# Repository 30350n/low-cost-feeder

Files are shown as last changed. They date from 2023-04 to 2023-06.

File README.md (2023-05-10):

# Low Co$t Feeder

This is a cost optimized version of the original LumenPnP Feeders by
[Opulo](https://www.opulo.io/).

## Warning: This is still highly experimental, PCBs haven't been ordered/tested at all yet.

### Changes:

- **3.3V -> 5V mcu/logic supply**  
  The original RS485 transceiver costs 6-7€ in Qty 10, alternative parts that can be powered
  by 3.3V start at 3-4€. Similar 5V powered parts are already available for ~1€.
- **STM32F031 -> ATmega328PB**  
  The ATmega328P is just the first MCU I could think of that's 5V compatible and has just enough
  IO, is available in similar packages (TQFP and QFN), is similarly priced and should be able to
  run the photon firmware just fine. The ATmega328PB is not a drop in replacement, but has extra
  features (like UUID support) and is even cheaper.
- **470uF -> 100uF buck converter output capacitor**  
  There are very few 470uF 10V capable caps available in the specified package. The 470uF cap
  is also very overspecd, 100uF should be totally sufficient for the application. (The original
  value probably got copied straight from the datasheet example schematic.)
- **Countersinks -> [24882 solderable standoffs](https://www.digikey.com/en/products/detail/keystone-electronics/24882/9921841)**  
  Getting the countersinks done by the PCB manufacturer is probably way to expensive,
  especially for low qty orders. The standoffs would add a cost of ~2.5€ per board.
  Alternatively it might be possible to use a 3D print with standard M3 nuts/heat set inserts,
  glued to the PCB in their place.  
  Adding the countersinks to the holes yourself is still possible too.
- **Option to bypass the onboard SMPS** (thanks @FL140 for the idea!)  
  Added a 0R resistor to bypass the onboard SMPS for **users of +12V machines**. This should
  save 1-2€ in components and might also have some other benefits, like better EMC.  
  **If this option is being used, the DRV8837 motor drivers should be replaced with +12V
  tolerant ones, for example DRV8220.**

## LumenPnP Feeders
The LumenPnP Feeders are open source pick and place feeders to aid in [Mid-Scale Manufacturing](https://stephenhawes.com/level-2-manufacturing/).

LumenPnP Feeders

LumenPnP Feeders are available for sale on the [Opulo Website](https://www.opulo.io/). If you build or buy one, please help the project by documenting bugs with a GitHub issue.

The LumenPnP Feeders run [Photon](https://github.com/photonfirmware/photon), an open source firmware project for pick and place feeders. The popular pick and place control software [OpenPnP](https://openpnp.org/) has Photon support built in, so it's easy to get going with the LumenPnP feeders using your existing OpenPnP setup. These feeders are designed to work with the [LumenPnP](https://opulo.io/products/lumenpnp).

The development process is being cataloged in a series of videos. A playlist of these can be found [here](https://www.youtube.com/playlist?list=PLIeJXmcg1baLBz3x0nCDqkYpKs2IWGHk4).

### Documentation
Feeder user documentation can be found on the [Opulo Docs Page](https://docs.opulo.io/). Open Hardware Assembly instructions can be found at [ohai.opulo.io](https://ohai.opulo.io/).

### Community
Discussion about the project happens on the [STR Discord server](https://discordapp.com/invite/TCwy6De)!

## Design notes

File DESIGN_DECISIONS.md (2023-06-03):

# LumenPnP Feeder Design Decisions

This page aims to illustrate the design decisions behind the LumenPnP Feeders. The design process started in early 2020, and has seen hundreds of iterations and approaches. This page gives background about why things are done the way they are, to help communicate to folks new to the project what has been tried, and why it was not chosen.

## Overview

The LumenPnP feeders are a mostly 3D printed tape feeder capable of reliably feeding 0402 components. They are designed to easily mount to a 20mm x 20mm v-slot aluminum extrusion. There are two motors in the system: a drive motor and a peel motor. The drive motor is a right-angle N20 motor with an encoder, giving us incredibly high resolution control of the motor's position. The peel motor is a standard N20 motor that peels film using a few 3D printed gears. The feeder has two buttons for tape loading and manual control. A third button puts the feeder into bootloader mode, allowing anyone to flash new firmware using a common FTDI USB to UART converter.

Feeders connect to power and communication when mounted to a rail through a "slot." Slots all connect back to a LumenPnP motherboard using an IDC cable. Each slot has a 1-Wire EEPROM onboard which holds the slot's address. This address is used to tell OpenPnP where a certain feeder has been mounted. All communication back to the motherboard happens over RS-485 using the Photon Protocol.

## Drive Subsystem

The Drive Subsystem is in charge of moving the tape forward at very precise increments. A right-angle N20 motor with a 1:1030 ratio gearbox was chosen for this task. This gear ratio provide a tremendous amount of torque for the size of the motor. An encoder on the back shaft of the motor has 14 ticks per revolution, which results in a theoretical 8.8 micron tape movement resolution. Of course, there are many other factors at play that reduce how precise the feeder is actually able to position tape, but the encoder is plenty precise enough for our application.

### Why not stepper motors?

While stepper motors are great for high-precision movement in systems like a 3D printer, they're less optimal for a small device like a feeder.

One of the main considerations with a feeder design is its width. The thinner a feeder is, the more of them you can fit on a given machine, and the more useful they become. Steppers thin enough to fit within a reasonably sized feeder suffer from a lack of torque, and would likely skip steps trying to advance tape. This is especially true when using microstepping, which would likely be necessary for the small movements required in a feeder.

Steppers also lack absolute positioning. All of their movements are relative, and without an encoder or a driver that supports skipped-step detection, we wouldn't know if the stepper has skipped steps.

It's possible to use a pancake stepper motor with a high-torque gearbox and a driver like the TMC2209 for skipped step detection, but a small DC motor with an encoder used fewer parts and had fewer points of failure.

### Why not an external gearbox/gear system?

Many feeder designs utilize a custom gear system that is mounted within the feeder itself. This can provide incredibly high torque if the gearing ratio is high enough.

We chose to avoid this for two main reasons. The first is that we trust the metal gearbox in a right-angle N20 motor much more than a (likely plastic) gear system that we designed. The N20 "standard" is ubiquitous and thoroughly tested. If we can keep our entire gearing system in metal gears, and in an easily sourced, highly tested part, it's a huge win for accessibility and reliability.

The second reason is ease of sourcing/building. If we used "off the shelf" nylon gears, not only would using a pre-existing gear be a huge design limitation, but also they might be difficult to source for the hobbyist or builder. If we went with totally custom gears, this makes the sourcing issue even worse. And even if folks could print them at home, the resolution required for the precise tape movement would be so high that the print would likely have to be SLA.

### Why not an encoder on the drive wheel itself?

In early versions of the feeder, we used a reflective sensor to watch for voids in the drive wheel. Putting our closed-loop feedback system on the last step of the drivetrain is great in theory. Monitoring as close to the actual metric you're controlling will provide a tighter coupling between your independent and dependent variables. There are three reasons we ended up switching to a magnetic encoder on the motor's back shaft.

The first is the low precision of the reflective sensor. The low/high and high/low threshold transition point of the reflective sensor was entirely dependent on how precise the cutout of the drive wheel was. Given that the wheels are made from PCBs which do not have a high tolerance with edge cuts, precision was very low. The sensor itself was also very noisy, requiring lots of signal processing to provide a useful signal. Early tests showed that *each feeder* would need its own custom calibration, which would be a tremendous effort, and discourage hacking.

On the other hand, a magnetic encoder provides 14 ticks per revolution of the motor. Because we are gearing down the motor with such a high ratio, we get an astronomically high precision of our gearbox output.

`14 ticks / 1 motor revolution * 1030 motor revolution / 1 gearbox revolution = 14420 ticks / 1 gearbox revolution`

This means that with a 128mm wheel circumference (32 teeth with 4mm spacing), we have a theoretical 8.877 micron tape positioning resolution. In practice, small tolerance stackups in the gearbox and drive wheel geometry mean we aren't this precise with actual tape position, but it's much better than the 200-500 or so micron resolution we saw with the reflective sensor.

The second reason is that any backlash error in the N20 gearbox can be accounted for by only positioning **from one side**. Backlash is only evident when there exists a reversal of the axis direction. If we only ever approach our position from one direction, backlash does not play into the tape positioning. Even when feeding backwards, we simply overshoot the final position, then approach again from the same direction.

The third reason is that with an encoder, we can move arbitrary distances. With a reflective sensor/slotted drive wheel, our resolution is limited to how far apart we've spaced the slots. With an encoder, we can command the feeder to move effectively any distance (provided it's a multiple of 8.877 microns!). This means feeding 1mm increments is fundamentally the same as feeding 4mm increments.

However, this all assumes that the encoder on the output wheel is comprised of a slotted PCB with a reflective sensor. Very thin encoder wheels and sensors exist, and might be a reasonable option for feeder tape positioning. We decided against this approach due to the lower resolution, cost, and likely need for customization that would make homebrew builds more difficult. They're also susceptible to errors due to light bleed.

### Why glue the shaft collar to the Drive Wheel?

Ideally, affixing the shaft collar to the Drive Wheel uses mechanical coupling, as glue can be finicky. We tried a screw-affixed design, but in order to have the screws fit without hitting the motor the PCB needed to be countersunk. That countersink added a bump to the opposite side of the board. When the shaft collar was mounted to it, we saw a very high sinusoidal variation in the tape position throughout the rotation of the wheel because the collar and wheel weren't coplanar anymore. Glue ended up being the most consistent approach in terms of tape positional accuracy.

We used to have a  D-shaft cutout in the center of the wheel, we found that it was over-constraining the glueing process so we removed it. If we're going to glue, we should reference it to the outer profile of the teeth as much as possible, which is really what matters in this application.

## Peel Subsystem

The Peel Subsystem is comprised of a standard N20 motor with a 1:210 gear ratio, with a printed worm gear attached to the output shaft. This worm gear interfaces with a gearbox used for peeling the film. The two straight gears that perform the peeling are mounted with a positive interface, ensuring the frame holding them in place is constantly applying pressure between them. This interface is what grips the film and pulls it away from the tape.

### Why not passive peeling?

Passive peeling mechanisms have been shown to work in many instances. Allowing the force of the drive motor to remove and/or guide the film away from the tape is a great way to reduce the part count. We ultimately decided to use a dedicated peel motor instead of a passive approach for a number of reasons.

First, in our tests we found that passive film peeling methods were only reliable with highly-tuned 3D printer settings to make a working geometry. Not only do we want the design to be possible to be built at home, but it also needs to be straightforward to build in a scaled-up manufacturing setting. Scrapping a high volume of prints because of not hitting a very tight dimensional tolerance would be a frustrating and expensive experience for builders and Opulo alike.

Second, we found that passive film peeling worked better with certain types of tape, and worse with others. In situations where the film is lightly attached to the tape, depending on the method of passive film removal, *both* sides of the film could come unstuck from the tape, jamming the feeder. In the situation where the adhesion was high between the film and tape, the drive motor had to work much, much harder to both drive the tape and remove the film.

Our approach not only ensures there's plenty of force present pulling the film from the tape, but it also accommodates any type of tape as defined by the EIA-418 standard. Even if the film is strongly adhered to the tape, or stretches easily and requires more peeling, the flexture holding the peel gears together allows film to slide between the gears when overdriven.

### Aren't you worried about wear/creep with plastic gears and tensioning?

At first, we were. But the benefits of being printable are high, allowing the design to be more accessible. We ran lifetime tests with the peel mechanism and had very good results.

We tested the peel gear box to a quarter million feed cycles, resulting in a kilometer of tape fed, and saw no failure of the gearbox's ability to peel film. There is slight initial wear of the gears that is present within the first 10k cycles, but after this the system hits steady-state.

Even then, we ensured that this part is easily replaceable if need be. It's easily printable at home, and can be replaced in less than a minute with only two screws.

### Why no tension sensor?

We found that it wasn't necessary. Many feeder designs use a switch to detect when the film has reached a sufficient tension, but with our flextured peel gear box, we can simply overdrive the peel mechanism and the film will slip through the gears once it's been peeled fully and can't move any more.

## Voltage Rails

The feeders are powered by 24 volts on the slot. They step this down to 10 volts using a buck converter, then down to 3.3 volts using an LDO.

### Why 24 Volts Bus Voltage?

24 volts was chosen for the bus voltage for a few reasons. First, it's already on the motherboard given that it's the voltage of the power supply for the machine. Second, a higher voltage allows us to send more power over thinner wire. We wanted to use IDC connectors on the slot harness due to the form factor of the slot, and need for many connectors on a single cable. Using 24 volts lets us send more power for a given current limit of the cable.

Next comes the 10 volt buck converter. The N20 motors accept up to 12 volts, but the DRV8837 H-Bridge motor driver chips only accept up to 11 volts. This chip was chosen as the motor driver due to its cost and availability. Other chips with a higher acceptable voltage of course exist, but are much more expensive or can be hard to source. We also looked for 24 volts motors, but the N20 standard does not seem to accept a voltage higher than 12 volts.

Lastly is the 3.3 volt LDO. This is used for the microcontroller, encoder, switches, LEDs, etc.

## Slot Addressing

Each feeder is loaded into a slot, which is a small 3D print and PCB with a 1-Wire EEPROM. When the feeder is loaded, it reads the slot address from the EEPROM. This is what the host uses to address the feeder in most instances.

### Why is this even necessary?

This system isn't strictly necessary for feeders to operate. But it does allow the host to be much more intelligent about how it handles feeders.

If we neglected to have a slot address, then we'd be operating purely on the feeder's UUID. Assuming we've solved the problem of feeder discovery once inserted, the host would have no idea *where* the feeder is after it's mounted. This means that the user needs to manually jog the head to the feeder every time it's inserted in order to set pick position.

If we neglected to have a feeder UUID and only knew what location a feeder was mounted into, we wouldn't be able to keep track of what part the feeder has; we'd just know where it is.

By having both a feeder UUID, and an address for each location, we can dynamically find where a feeder has been inserted and know what part is at that location.

### Why not use voltage dividers?

Voltage dividers are a very inexpensive method of setting a specific value for a microcontroller. The EEPROM might seem like overkill to hold a single address. We chose to avoid voltage dividers for a couple reasons.

Firstly, the likelihood of error was very high. If we want to support up to 255 devices on the bus, we'd need that many addresses, and that many discrete voltages from the divider. With a 3.3 volt starting voltage, that means we have 12.9 millivolts per address. The precision of the resistors used would have to be incredibly high to support this resolution, and we'd be assuming no voltage loss in the spring-pin interface.

Voltage dividers also require that the feeder has an ADC as opposed to just a GPIO pin used for 1-Wire communication.

### Why not use an I2C/SPI EEPROM?

Provided that we were able to find a spring pin connector with two more wires, we absolutely could have! The benefit of 1-Wire is that it only requires one pin for both communication *and* power. I2C devices would require three dedicated pins: SDA, SCL, and VCC. The spring pin interface we chose that allows the entire feeder geometry to work only comes with up to 5 pins. With four already used for RS-485 and power, the one left is allocated to the EEPROM.

## Host Communication

At the top of the communication stack is the host. The host is what decides which feeder needs to feed, and when. OpenPnP acts as the host in this scenario. OpenPnP sends M485 commands to Marlin, and gets data from feeders back as a result. A custom OpenPnP feeder type `PhotonFeeder` supports common Photon commands such as feed, self-identify, initialize, or check for feed status.

Next comes Marlin. Marlin is the firmware on the LumenPnP and relays commands to feeders along an RS-485 bus that connects to every slot. It sends data using the Photon Protocol. A new M command for Marlin's gcode interface, M485, allows a host to send data down the RS-485 bus using Photon, and thereby communicating with feeders.

### Why RS-485?

RS-485 is an electrical standard that is widely used, particularly in industrial environments. Being a differential signal, electromagnetic interference that affects both data lines does not affect the signal integrity.

### Why not CAN?

CAN would have also been a great option for feeder communication. The decision to stick with a custom protocol over RS-485 ended up coming down to the large size of a CAN frame. The arbitration system is a bit overkill for a system with only two types of devices. Bit stuffing, plus a long CRC and end of frame section make the frame lengthy, keeping the bus noisier than necessary. CAN would have worked just fine, we just preferred to spin our own protocol that was exactly what we needed.

### Why not MODBUS?

MODBUS is a great, royalty-free protocol, and does fulfill many project requirements. There are two main reasons we decided to implement our own protocol.

The first is that MODBUS only supports the host initiating a message. We wanted to allow the possibility that feeders themselves can initiate communication back to the host, instead of only ever waiting to be queried.

The second reason is that we are not only working with a device ID, we are working with its slot address, which acts as its location on the machine. Although we could store address data in the feeder and query it with MODBUS, we couldn't scan every possible feeder ID easily. With Photon, we simply ping each of the 50 possible addresses and see which IDs come back. MODBUS is designed for systems where the ID of each device on the bus is known, and likely immutable. Feeders are easily swapped, and need to be easily recognized once inserted. This flexibility is what Photon provides.

## Microcontroller

An STM32F031C6T6 was chosen for the feeder's microcontroller. There were a few requirements of the chip in order to hit the project goals:

* Available and generally low cost (two variables that are a moving target in our modern semiconductor market)
* At least 1 UART for RS-485
* Sufficient GPIO for buttons, LED, encoder, etc.
* Internal UUID for identification by the host

As a bonus, the chip's sibling, the STM32F031K6U6, has the same die as the C6T6 but with a smaller package. This means that by using the smaller chip's GPIO count as a constraint, we have a binary-compatible drop in replacement part to help alleviate availability issues.

Although a separate EEPROM chip or a software-defined UUID could solve the same problem as having a factory-burned UUID, having it in the chip prevents UUID erasure upon reprogramming, and fewer parts in the BOM.

## ID Fiducial Board

There's a small board on the nose of the feeder with three fiducials on it. The center one is for identifying location, and the other, smaller fiducials on either side identify what type of feeder it is.

**This is not currently used. This board was shipped with all feeder hardware to support potential future features.**

### Can it be used for setting pick position?

It could be used for *generalized* pick position. In general, there's too much variability in the precise placement of the PCB in the print from human error and print defects. If OpenPnP can scan for the fiducial and then apply a general offset to find the broad pick position, computer vision can find the precise pick position, provided it's paper tape. Plastic tape would likely need the precise pick position set manually.

### Can it be used for identifying feeder width?

Absolutely! The distance the two smaller fiducials are away from the larger centered one encodes what feeder type, or width, it is. Ideally the firmware image is the same across feeder widths, and it can't hurt to have the fiducial encode that information. OpenPnP doesn't actually care that much what width a feeder is if the fiducial <-> pick position offset is set correctly.

### Can it be used for setting slot location?

It can, but it might not be useful in most circumstances. In a world where slots are always mounted in the same location, OpenPnP could always know where the slot locations are on a LumenPnP. However, if builders have a different slot setup, or folks trying to squeeze out every last mm of feeder space are adjusting their slot locations to accommodate wider feeders, it could be useful. OpenPnP could use vision across a given Y position and in conjunction with the slot addresses of the feeders it found over RS485, automatically set slot positions.

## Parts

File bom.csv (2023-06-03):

Part Name | Image | Quantity | Part Type | Source 1 | Source 2 | Optional | Note
frame |  | 1 | FDM | Download all 3D printed parts at the link at the top of the page.
drive-motor-bracket |  | 1 | FDM | Download all 3D printed parts at the link at the top of the page.
drive-motor-cover |  | 1 | FDM | Download all 3D printed parts at the link at the top of the page.
peel-gear-frame |  | 1 | FDM | Download all 3D printed parts at the link at the top of the page.
peel-gear |  | 2 | FDM | Download all 3D printed parts at the link at the top of the page.
peel-worm-gear |  | 1 | FDM | Download all 3D printed parts at the link at the top of the page.
release-lever |  | 1 | FDM | Download all 3D printed parts at the link at the top of the page.
spool-holder |  | 1 | FDM | Download all 3D printed parts at the link at the top of the page.
thimble |  | 1 | FDM | Download all 3D printed parts at the link at the top of the page.
slot-bracket |  | 1 | FDM | Download all 3D printed parts at the link at the top of the page.
PLA-filament | https://90a1c75758623581b3f8-5c119c3de181c9857fcb2784776b17ef.ssl.cf2.rackcdn.com/611532_989269_03_front_zoom.jpg | 1.2 | FIL | https://www.microcenter.com/product/611532/inland-175mm-black-pla-3d-printer-filament-1kg-spool-(22-lbs) |  |  | Units in kg. Print both nozzle-rack and 2x z-gantry in a black color. Print top-light-mount and bottom-light-mount in a white color.
M3-hex-nut | https://www.mcmaster.com/mvD/Contents/gfx/ImageCache/905/90592A085p1-b01-digitall@4x_636713274654410000.png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 | 11 | FST | https://www.mcmaster.com/90592A085/ |  |  | ISO4032
M5-t-slot-nut | https://www.mcmaster.com/mvD/Contents/gfx/ImageCache/946/94645a102-@1x_637691238154449529.png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 | 1 | FST | https://www.mcmaster.com/94645A102/
M3x12mm-flat-head | https://www.mcmaster.com/mvD/Contents/gfx/ImageCache/920/92095A181p1-b01-digitall@2x_636621119072096469.png | 2 | FST | https://www.mcmaster.com/92095A181/
M3x14mm-flat-head | https://www.mcmaster.com/mvD/Contents/gfx/ImageCache/920/92095A168p1-b01-digitall@2x_636621121852034289.png | 2 | FST | https://www.mcmaster.com/92095A168/
M3x15mm-flat-head | https://www.mcmaster.com/mvC/Contents/gfx/ImageCache/912/91292a115-@4x_637619456157301135.png | 10 | FST | https://www.mcmaster.com/91292A115
M5x10mm-socket-head | https://www.mcmaster.com/mvD/Contents/gfx/ImageCache/901/90128a234-@4x_637648793587366175.png | 1 | FST | https://www.mcmaster.com/90128A234/ |  |  | ISO4762
M3x8mm-self-tapping-flat-head | https://www.mcmaster.com/mvD/Contents/gfx/ImageCache/958/95893a189_5471d27b-8a4e-4cd5-bc6c-43c4b611d281@2x_637901339772075158.png | 1 | FST | https://www.mcmaster.com/95893A189/
mobo |  | 1 | PCA |  |  |  | Click link above to download source. 1.6mm PCB, 2 layer, Black Soldermask, White Silkscreen, ENIG
slot |  | 1 | PCA |  |  |  | Click link above to download source. 1.6mm PCB, 2, layer, Black Soldermask, White Silkscreen, ENIG
drive-wheel |  | 1 | PCB |  |  |  | Click link above to download source. 1mm PCB, 2 layer, Any Color Soldermask, White Silkscreen, ENIG
light-diffusion |  | 1 | PCB |  |  |  | Click link above to download source. 0.6mm PCB, 2 layer, Matte Black Soldermask. Board has no silkscreen or copper. Only soldermask on the front and back.
photon-8mm-fid |  | 1 | PCB |  |  |  | Click link above to download source. 1mm PCB, 2 layer, Matte Black Soldermask, White Silkscreen, ENIG
slot-harness |  | 1 | CHA |  |  |  | Click link above to download source
spring | https://www.leespring.com/sites/default/files/inline-images/226%C3%97113_Compression_HomePage_2.jpg | 1 | MISC | https://www.leespring.com/compression-springs?search=LC026C06M
n20-motor | https://www.makerfabs.com/image/cache/makerfabs/N20%20DC%20Gear%20Motor/N20%20DC%20Gear%20Motor_3-1000x750.jpg | 4 | MISC | https://www.servocity.com/110-rpm-micro-gear-motor/ |  |  | 1:210 gear ratio.
right-angle-n20 | https://sharvielectronics.com/wp-content/uploads/2022/06/N20-3V-50-RPM-Micro-Metal-Gear-Motor-With-Encoder_-Sharvielectronics.jpg | 2 | MISC | https://www.aliexpress.com/w/wholesale-worm-n20-encoder.html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 |  |  | 14-tick per revolution encoder. 1:1030 gear ratio gearbox.
shaft-collar | https://m.media-amazon.com/images/I/51dc5w8vG5L._AC_.jpg | 2 | MISC | https://www.amazon.com/gp/product/B01EA912P8/ref=ppx_yo_dt_b_asin_title_o09_s00?ie=UTF8

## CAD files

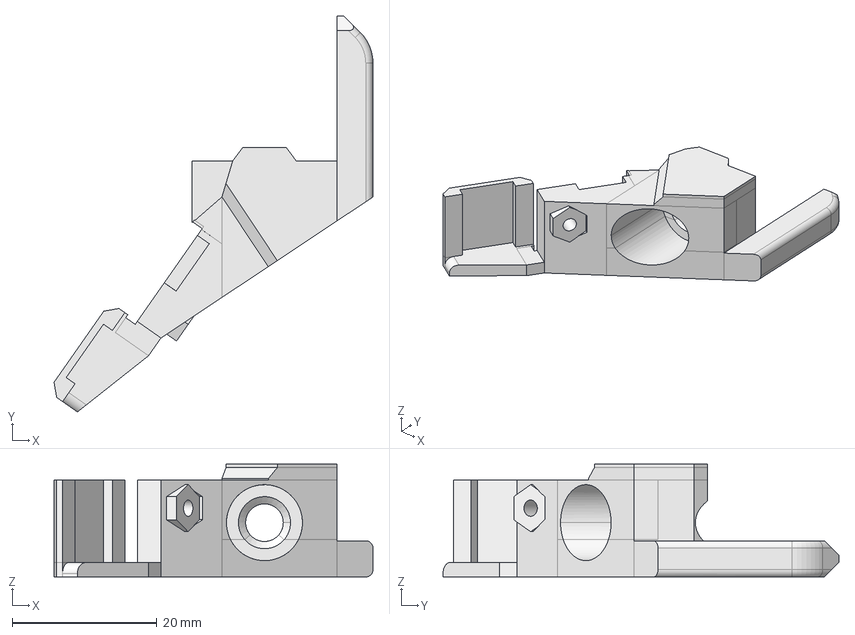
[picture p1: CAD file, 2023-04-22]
cad/FDM/slot-bracket.FCStd
44.1 x 54.7 x 15.6 mm

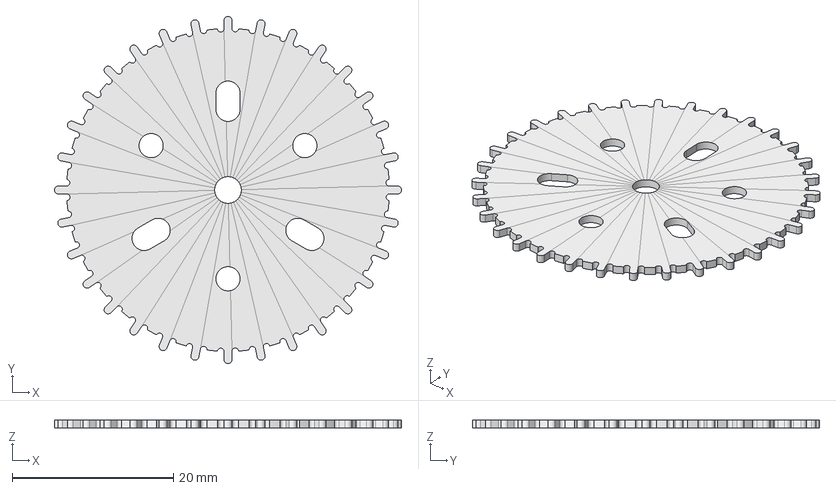
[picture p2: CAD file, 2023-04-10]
cad/indexing-wheel.FCStd
43.0 x 43.0 x 1.00 mm

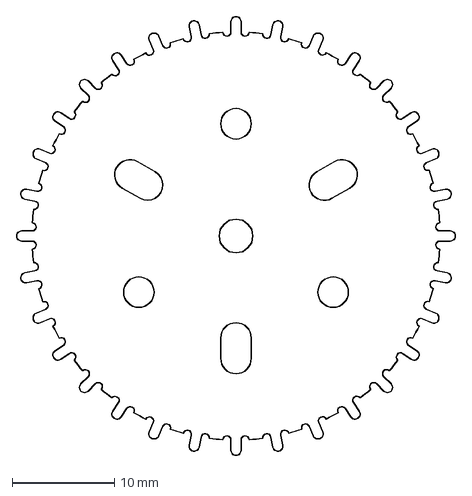
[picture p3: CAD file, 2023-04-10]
pcb/indexingWheel/indexingWheel-outline-rev06.dxf
43.0 x 43.0 mm

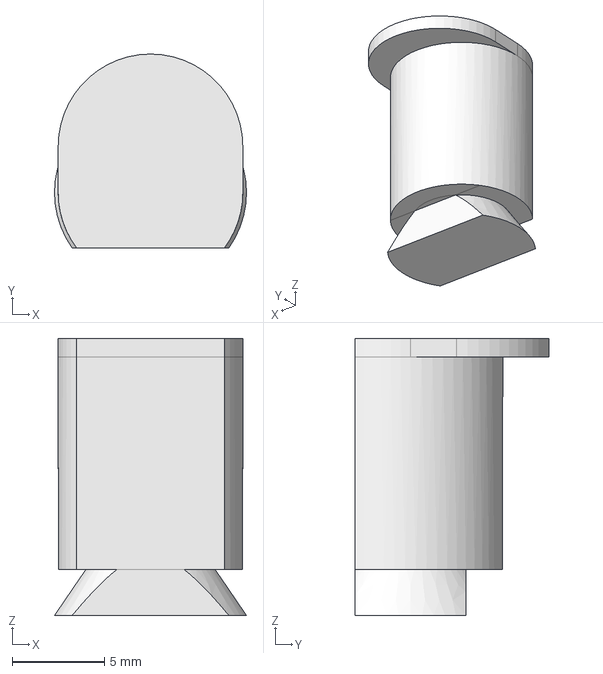
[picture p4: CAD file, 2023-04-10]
cad/FDM/thimble.FCStd
10.4 x 10.5 x 15.0 mm

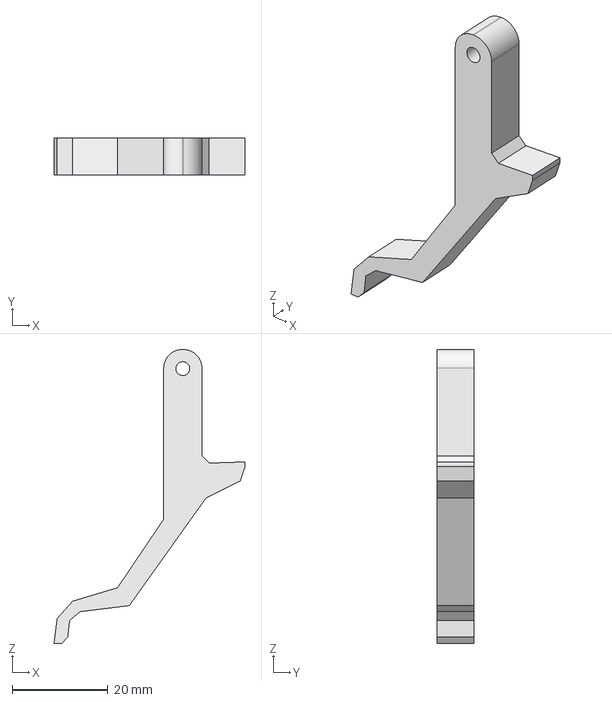
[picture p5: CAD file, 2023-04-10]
cad/FDM/release-lever.FCStd
39.9 x 7.75 x 61.5 mm

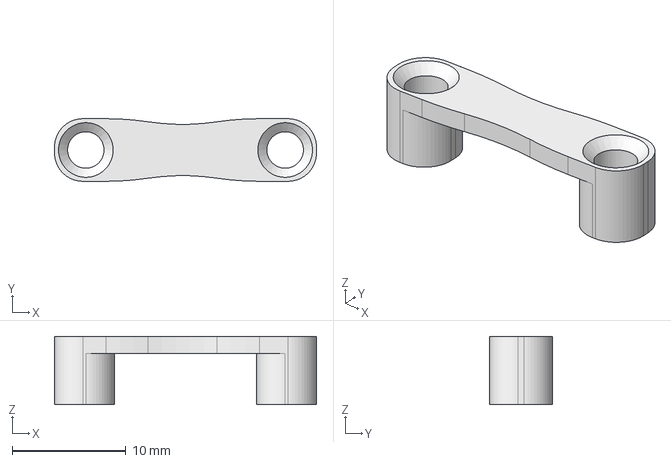
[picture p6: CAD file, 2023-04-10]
cad/FDM/drive-motor-bracket.FCStd
23.0 x 5.50 x 6.00 mm

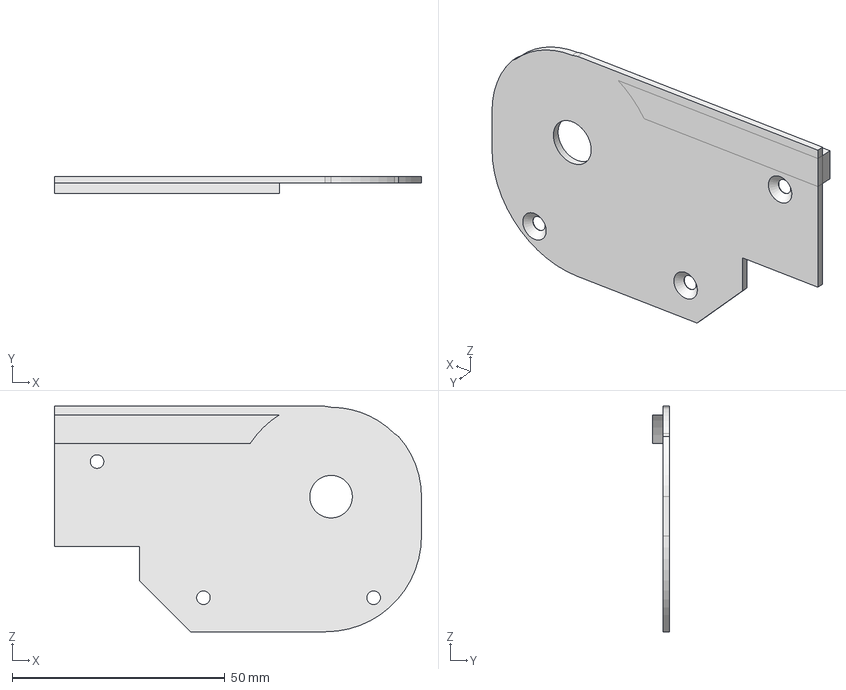
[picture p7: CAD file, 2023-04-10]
cad/FDM/drive-motor-cover.FCStd
86.2 x 4.10 x 53.0 mm

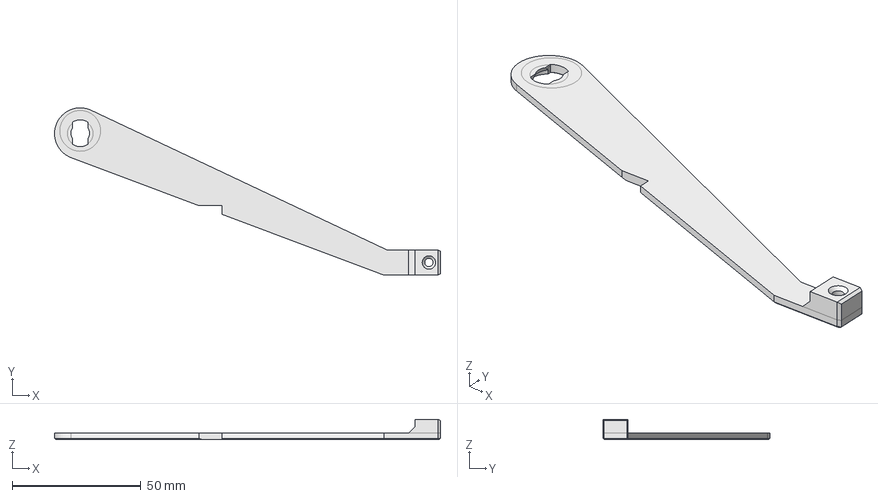
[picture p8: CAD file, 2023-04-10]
cad/FDM/spool-holder.FCStd
150.0 x 65.0 x 7.90 mm

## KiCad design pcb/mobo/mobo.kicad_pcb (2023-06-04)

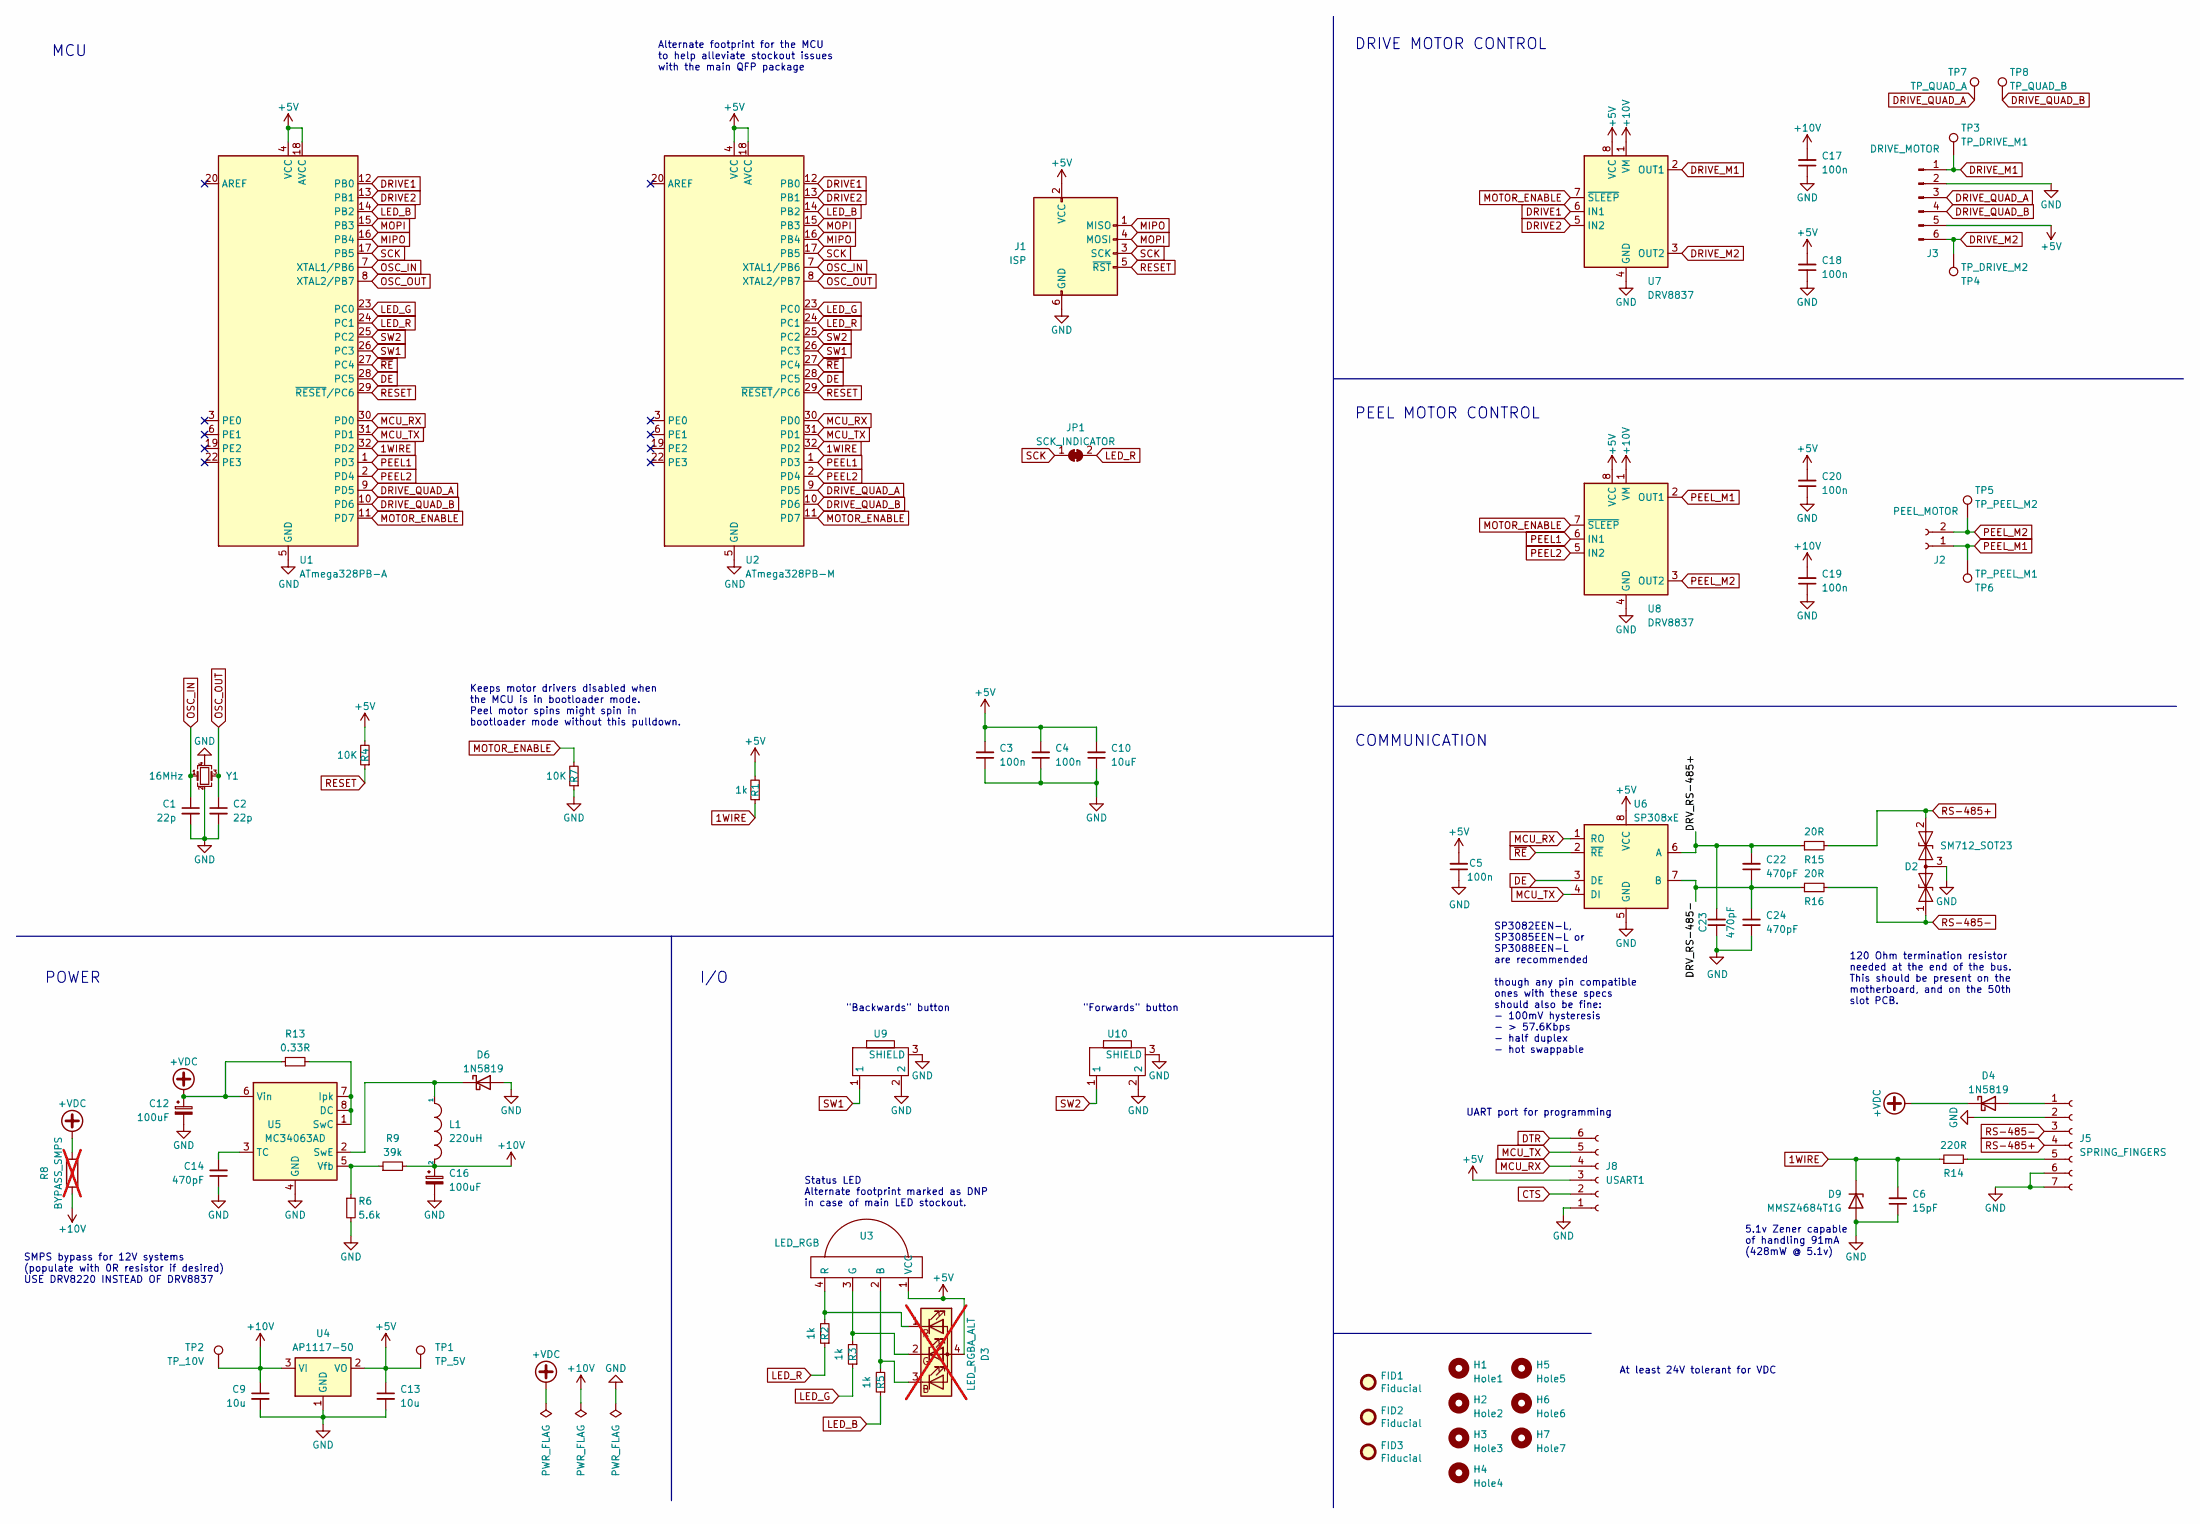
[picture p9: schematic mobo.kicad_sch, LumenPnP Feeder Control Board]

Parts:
C1, C2: 22p; C_0805_2012Metric; JLCPCB C1794
C3, C4, C5, C17, C18, C19, C20: 100n; C_0805_2012Metric; JLCPCB C49678
C6: 15pF; C_0805_2012Metric; JLCPCB C49678
C9, C13: 10u; C_0805_2012Metric; JLCPCB C15850
C10: 10uF; C_0805_2012Metric; JLCPCB C49678
C12, C16: 100uF; C_Elec_6.3x7.7
C14, C22, C23, C24: 470pF; C_0805_2012Metric; JLCPCB C49678
D2: SM712_SOT23; SOT-23; LCSC C521963
D3: LED_RGBA_ALT; LED_LiteOn_LTST-C19HE1WT; not fitted
D4, D6: 1N5819; D_SOD-123
D9: MMSZ4684T1G; D_SOD-123; JLCPCB MMSZ4684T1G
FID1, FID2, FID3: Fiducial; Fiducial_1mm_Mask2mm
H1: Hole1; MountingHole_4.2mm_24822
H2: Hole2; MountingHole_4.2mm_24822
H3: Hole3; MountingHole_4.2mm_24822
H4: Hole4; MountingHole_4.2mm_24822
H5: Hole5; MountingHole_4.2mm_24822
H6: Hole6; MountingHole_4.2mm_24822
H7: Hole7; MountingHole_4.2mm_24822
J1: ISP; ISP_FRICTION_FIT
J2: PEEL_MOTOR; Molex_PicoBlade_53261-0271_1x02-1MP_P1.25mm_Horizontal; LCSC C2845379
J3: DRIVE_MOTOR; Molex_PicoBlade_53261-0671_1x06-1MP_P1.25mm_Horizontal; LCSC C2845383
J5: SPRING_FINGERS; AVX-9155-005-541
J8: USART1; UART_FRICTION_FIT
JP1: SCK_INDICATOR; SolderJumper-2_P1.3mm_Bridged_RoundedPad1.0x1.5mm
L1: 220uH; L_6.3x6.3_H3; LCSC C467145
R1: 1k; R_0805_2012Metric; JLCPCB C17513
R2, R3, R5: 1k; R_0805_2012Metric; JLCPCB C17710
R4, R7: 10K; R_0805_2012Metric; JLCPCB C17513
R6: 5.6k; R_0805_2012Metric
R8: BYPASS_SMPS; R_0805_2012Metric; not fitted
R9: 39k; R_0805_2012Metric
R13: 0.33R; R_0805_2012Metric
R14: 220R; R_0805_2012Metric
R15, R16: 20R; R_0805_2012Metric
TP1: TP_5V; TestPoint_Pad_D2.0mm
TP2: TP_10V; TestPoint_Pad_D2.0mm
TP3: TP_DRIVE_M1; TestPoint_Pad_D2.0mm
TP4: TP_DRIVE_M2; TestPoint_Pad_D2.0mm
TP5: TP_PEEL_M2; TestPoint_Pad_D2.0mm
TP6: TP_PEEL_M1; TestPoint_Pad_D2.0mm
TP7: TP_QUAD_A; TestPoint_Pad_D2.0mm
TP8: TP_QUAD_B; TestPoint_Pad_D2.0mm
U1: ATmega328PB-A; TQFP-32_7x7mm_P0.8mm
U2: ATmega328PB-M; QFN-32-1EP_5x5mm_P0.5mm_EP3.1x3.1mm_DNP
U3: LED_RGB; MHS110FRGBCT
U4: AP1117-50; SOT-223-3_TabPin2
U5: MC34063AD; SOIC-8_3.9x4.9mm_P1.27mm
U6: SP308xE; SOIC-8_3.9x4.9mm_P1.27mm
U7, U8: DRV8837; WSON-8-1EP_2x2mm_P0.5mm_EP0.9x1.6mm
U9, U10: 1TS003B-1400-3500A-CT
Y1: 16MHz; Crystal_SMD_3225-4Pin_3.2x2.5mm_HandSoldering; JLCPCB C253751

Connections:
1WIRE: C6.2, D9.1 (K), R1.1, R14.1, U1.32 (PD2), U2.32 (PD2)
+5V: C3.2, C4.2, C5.2, C10.2, C13.1, C18.2, C20.2, D3.4 (A), J1.2 (VCC), J3.5, J8.3, R1.2, R4.2, TP1.1, U1.4 (VCC), U1.18 (AVCC), U2.4 (VCC), U2.18 (AVCC), U3.1 (VCC), U4.2 (VO), U6.8 (VCC), U7.8 (VCC), U8.8 (VCC)
+10V: C9.1, C16.1, C17.2, C19.2, L1.2, R8.2, R9.2, TP2.1, U4.3 (VI), U7.1 (VM), U8.1 (VM)
+VDC: C12.1, D4.1 (K), R8.1, R13.1, U5.6 (Vin)
/DRV_RS-485+: C22.2, C23.2, R15.1, U6.6 (A)
/DRV_RS-485-: C22.1, C24.2, R16.1, U6.7 (B)
CTS: J8.2
DE: U1.28 (PC5), U2.28 (PC5), U6.3 (DE)
DRIVE1: U1.12 (PB0), U2.12 (PB0), U7.6 (IN1)
DRIVE2: U1.13 (PB1), U2.13 (PB1), U7.5 (IN2)
DRIVE_M1: J3.1, TP3.1, U7.2 (OUT1)
DRIVE_M2: J3.6, TP4.1, U7.3 (OUT2)
DRIVE_QUAD_A: J3.3, TP7.1, U1.9 (PD5), U2.9 (PD5)
DRIVE_QUAD_B: J3.4, TP8.1, U1.10 (PD6), U2.10 (PD6)
DTR: J8.6
GND: C1.2, C2.2, C3.1, C4.1, C5.1, C6.1, C9.2, C10.1, C12.2, C13.2, C14.1, C16.2, C17.1, C18.1, C19.1, C20.1, C23.1, C24.1, D2.3 (common), D6.2 (A), D9.2 (A), J1.6 (GND), J3.2, J5.2, J5.6, J5.7, J8.1, R6.2, R7.1, U1.5 (GND), U1.21 (GND), U2.5 (GND), U2.21 (GND), U2.33 (GND), U4.1 (GND), U5.4 (GND), U6.5 (GND), U7.4 (GND), U7.9 (GND), U8.4 (GND), U8.9 (GND), U9.2, U9.3 (SHIELD), U10.2, U10.3 (SHIELD), Y1.2, Y1.4
LED_B: R5.1, U1.14 (PB2), U2.14 (PB2)
LED_G: R3.1, U1.23 (PC0), U2.23 (PC0)
LED_R: JP1.2 (B), R2.1, U1.24 (PC1), U2.24 (PC1)
MCU_RX: J8.4, U1.30 (PD0), U2.30 (PD0), U6.1 (RO)
MCU_TX: J8.5, U1.31 (PD1), U2.31 (PD1), U6.4 (DI)
MIPO: J1.1 (MISO), U1.16 (PB4), U2.16 (PB4)
MOPI: J1.4 (MOSI), U1.15 (PB3), U2.15 (PB3)
MOTOR_ENABLE: R7.2, U1.11 (PD7), U2.11 (PD7), U7.7 (~SLEEP), U8.7 (~SLEEP)
unnamed: D3.3 (BK), R5.2, U3.2 (B)
unnamed: D3.2 (GK), R3.2, U3.3 (G)
unnamed: D3.1 (RK), R2.2, U3.4 (R)
unnamed: D4.2 (A), J5.1
unnamed: D6.1 (K), L1.1, U5.2 (SwE)
unnamed: J5.5, R14.2
unnamed: R13.2, U5.1 (SwC), U5.7 (Ipk), U5.8 (DC)
unnamed: C14.2, U5.3 (TC)
unnamed: R6.1, R9.1, U5.5 (Vfb)
OSC_IN: C1.1, U1.7 (XTAL1/PB6), U2.7 (XTAL1/PB6), Y1.1
OSC_OUT: C2.1, U1.8 (XTAL2/PB7), U2.8 (XTAL2/PB7), Y1.3
PEEL1: U1.1 (PD3), U2.1 (PD3), U8.6 (IN1)
PEEL2: U1.2 (PD4), U2.2 (PD4), U8.5 (IN2)
PEEL_M1: J2.1, TP6.1, U8.2 (OUT1)
PEEL_M2: J2.2, TP5.1, U8.3 (OUT2)
RESET: J1.5 (~RST), R4.1, U1.29 (~RESET/PC6), U2.29 (~RESET/PC6)
RS-485+: D2.2 (A2), J5.4, R15.2
RS-485-: D2.1 (A1), J5.3, R16.2
SCK: J1.3 (SCK), JP1.1 (A), U1.17 (PB5), U2.17 (PB5)
SW1: U1.26 (PC3), U2.26 (PC3), U9.1
SW2: U1.25 (PC2), U2.25 (PC2), U10.1
~RE: U1.27 (PC4), U2.27 (PC4), U6.2 (~RE)

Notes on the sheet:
SMPS bypass for 12V systems (populate with 0R resistor if desired) USE DRV8220 INSTEAD OF DRV8837
"Backwards" button
DRIVE MOTOR CONTROL
Status LED Alternate footprint marked as DNP in case of main LED stockout.
PEEL MOTOR CONTROL
120 Ohm termination resistor needed at the end of the bus. This should be present on the motherboard, and on the 50th slot PCB.
I/O
MCU
SP3082EEN-L, SP3085EEN-L or SP3088EEN-L are recommended though any pin compatible ones with these specs should also be fine: - 100mV hysteresis - > 57.6Kbps - half duplex - hot swappable
5.1v Zener capable of handling 91mA (428mW @ 5.1v)
"Forwards" button
At least 24V tolerant for VDC
Keeps motor drivers disabled when the MCU is in bootloader mode. Peel motor spins might spin in bootloader mode without this pulldown.
POWER
Alternate footprint for the MCU to help alleviate stockout issues with the main QFP package
UART port for programming
COMMUNICATION

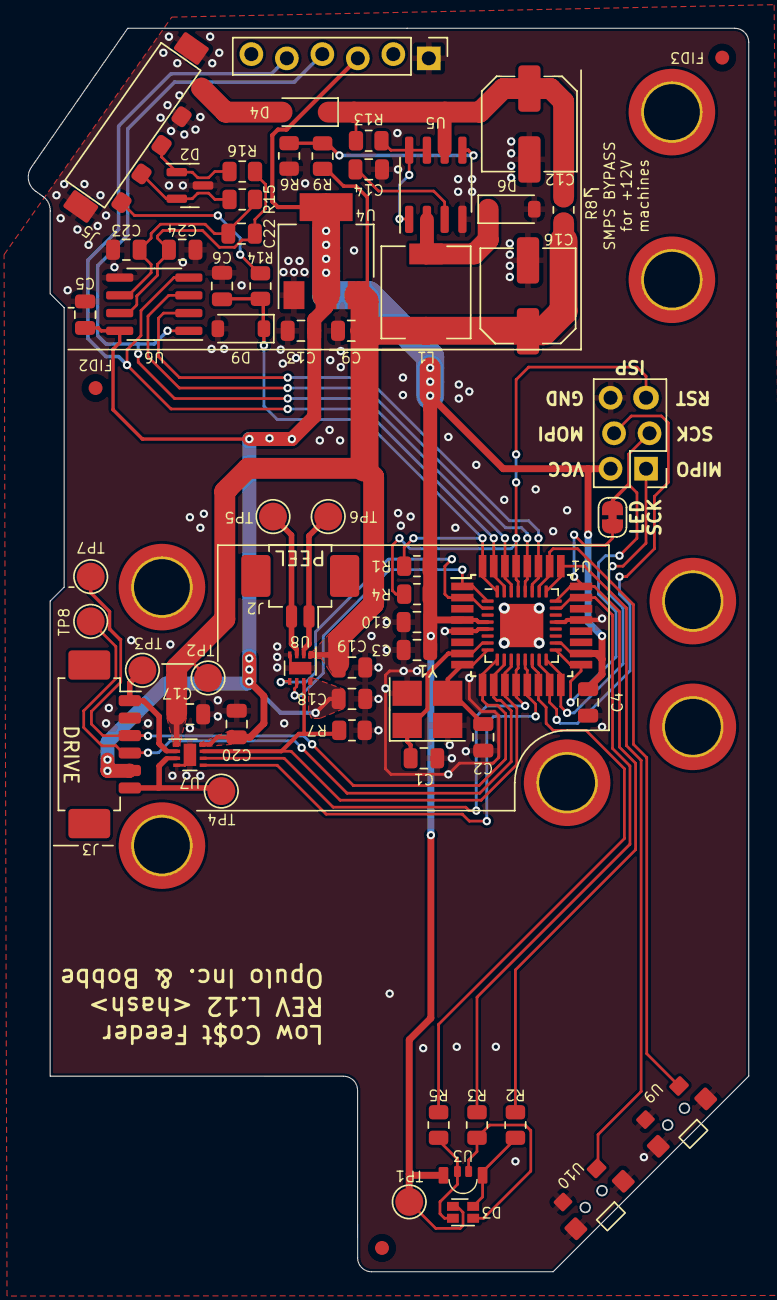
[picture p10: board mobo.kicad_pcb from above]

Board: 2 copper layers, 51.6 x 89.0 mm, 73 parts (0 on the bottom side), 44 nets.

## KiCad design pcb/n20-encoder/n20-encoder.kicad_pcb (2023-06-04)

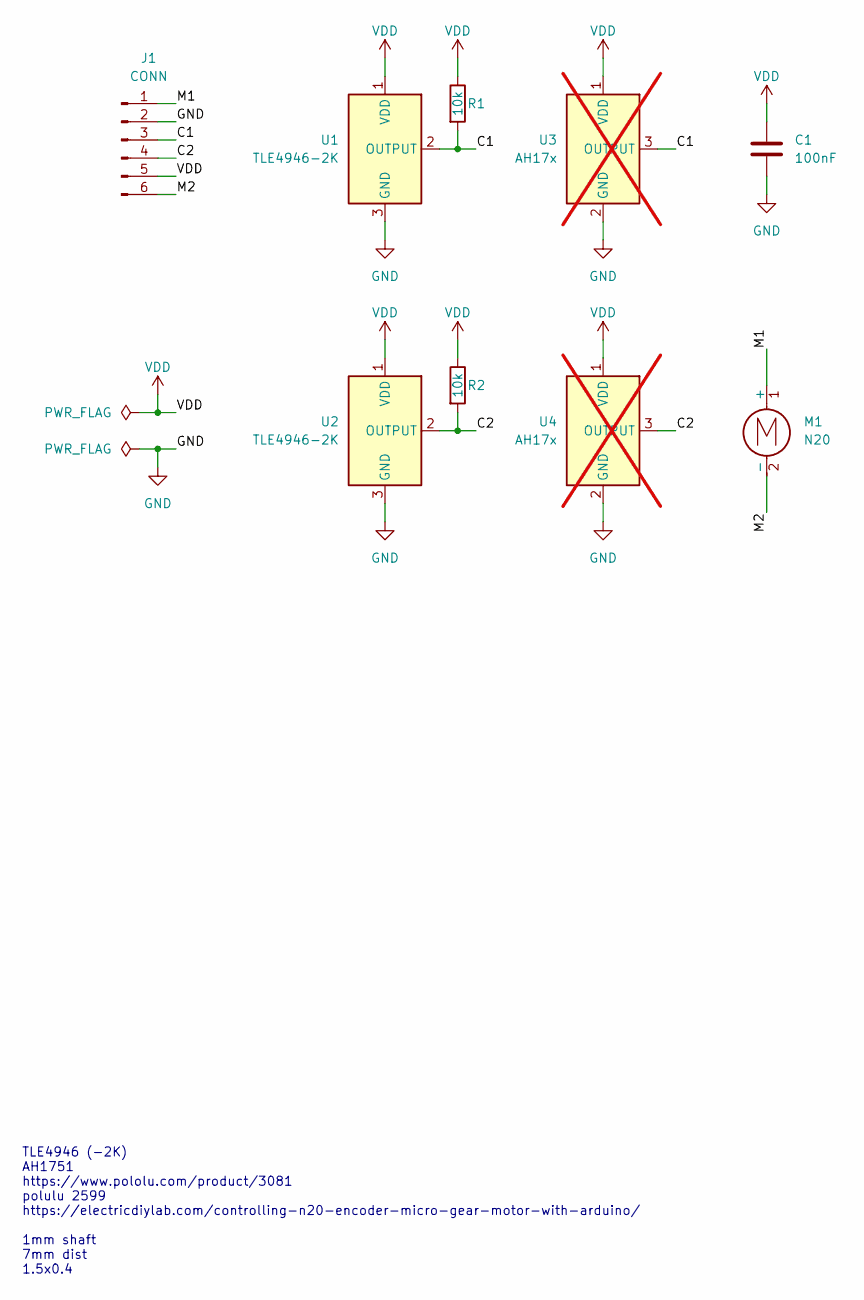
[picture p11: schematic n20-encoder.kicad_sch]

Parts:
C1: 100nF; C_0603_1608Metric
J1: CONN; JST_ZH_B6B-ZR-A_1x06_P1.50mm_Vertical
M1: N20; CHF-GW12T-N20VA
R1, R2: 10k; R_0603_1608Metric
U1, U2: TLE4946-2K; SC-59
U3, U4: AH17x; SIP-3_4.1x1.5mm_P1.27mm; not fitted

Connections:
/C1: J1.3, R1.2, U1.2 (OUTPUT), U3.3 (OUTPUT)
/C2: J1.4, R2.2, U2.2 (OUTPUT), U4.3 (OUTPUT)
/M1: J1.1, M1.1 (+)
/M2: J1.6, M1.2 (-)
GND: C1.2, J1.2, U1.3 (GND), U2.3 (GND), U3.2 (GND), U4.2 (GND)
VDD: C1.1, J1.5, R1.1, R2.1, U1.1 (VDD), U2.1 (VDD), U3.1 (VDD), U4.1 (VDD)

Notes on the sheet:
TLE4946 (-2K) AH1751 https://www.pololu.com/product/3081 polulu 2599 https://electricdiylab.com/controlling-n20-encoder-micro-gear-motor-with-arduino/ 1mm shaft 7mm dist 1.5x0.4

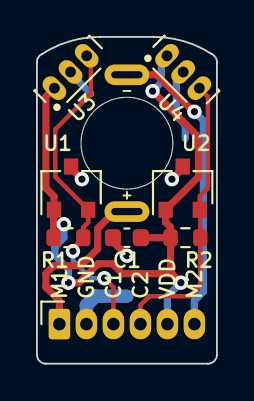
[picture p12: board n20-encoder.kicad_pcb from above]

Board: 2 copper layers, 10.0 x 18.2 mm, 9 parts (0 on the bottom side), 6 nets.

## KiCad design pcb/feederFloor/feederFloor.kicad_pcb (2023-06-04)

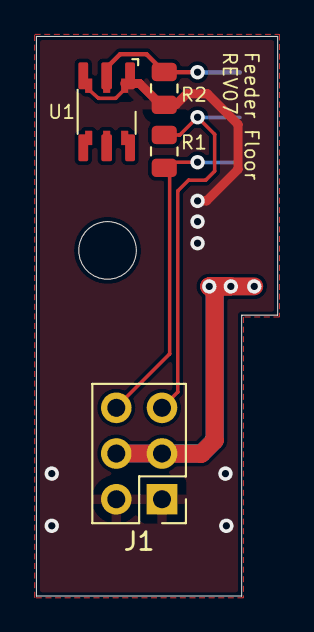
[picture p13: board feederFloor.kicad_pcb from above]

Board: 2 copper layers, 13.4 x 31.1 mm, 6 parts (1 on the bottom side), 5 nets.

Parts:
H1: MountingHole; MountingHole_3.2mm_M3
J1: IDC; PinHeader_2x03_P2.54mm_Vertical
J2: Conn_01x05_Female; AVX-915-005-541-Contact-Surface
R1: 120R; R_0805_2012Metric
R2: 1M; R_0805_2012Metric
U1: DS28E07; DS28E07_MULTI

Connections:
1WIRE: J2.1, R2.1, U1.2 (IO)
GND: J1.1, J1.2, J2.4, R2.2, U1.1 (GND)
RS-485+: J1.5, J2.2, R1.2
RS-485-: J1.6, J2.3, R1.1
VIN: J1.3, J1.4, J2.5

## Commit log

2023-04-05 Cost optimize main feeder pcb
    - Change mcu/logic supply to 5V instead of 3.3V
    - Use atmega328p as mcu
    - Use SP308xE as RS485 transceiver
    - Use 100uF output capacitor for buck coverter
    - Make it possible to use solderable standoffs instead of chamfers
    [mobo.kicad_pcb, mobo.kicad_sch]
2023-04-06 Fix standoff link in README
2023-04-25 Add decoupling cap for RS-485 transceiver, Set edge clearance to 0.2mm
    [mobo.kicad_pcb, mobo.kicad_sch]
2023-04-25 Add n20 encoder board
    [n20-encoder.kicad_pcb, n20-encoder.kicad_sch]
2023-04-26 Add diode for reverse polarity protection, Add SMPS bypass jumper
    [mobo.kicad_pcb, mobo.kicad_sch]
2023-04-26 Replace bypass jumper with 0R resistor
    [mobo.kicad_pcb, mobo.kicad_sch]
2023-05-10 Cleanup tracks and vias
    [mobo.kicad_pcb]
2023-05-10 Replace ATmega328P with ATmega328PB and improve RS-485 routing
    [mobo.kicad_pcb, mobo.kicad_sch]
2023-06-02 Replace n20-encoder edge cuts hole with drill, improve routing
    [n20-encoder.kicad_pcb]
2023-06-03 Remove vias from pads, Remove paste layer from alt QFN footprint (#14)
    [mobo.kicad_pcb, mobo.kicad_sch]
2023-06-03 Mark LED_RGBA_ALT as DNP, Add MHS110FRGBCT symbol, footprint (#9)
    [mobo.kicad_pcb, mobo.kicad_sch]
2023-06-03 Improve driver power routing by adding filled zones
    [mobo.kicad_pcb]
2023-06-03 Add X and Y caps to RS485 lines (#19), Update symbols
    [mobo.kicad_pcb, mobo.kicad_sch]
2023-06-03 Add push button symbol, Update footprints, Cleanup tracks
    [mobo.kicad_pcb, mobo.kicad_sch]
2023-06-03 Rearrange schematic and add annotations
    [mobo.kicad_sch]
2023-06-03 Remove copper pour from spring finger protector
    [mobo.kicad_pcb]
2023-06-03 Cleanup silkscreen
    [mobo.kicad_pcb]
2023-06-03 Add keepout area for counter sinks to mounting holes
    [mobo.kicad_pcb]
2023-06-03 Update .gitignore to KiCad 7.0, Remove backup, prl files
2023-06-03 Invert light diffusion board logo, fix lib table
    [light-diffusion.kicad_pcb]
2023-06-04 Fix plot settings for light diffusion board (prev. commit fixed #33)
    [light-diffusion.kicad_pcb]
2023-06-04 Fix indexing wheel design rules, Set stackup, plot settings
    [indexingWheel.kicad_pcb]
2023-06-04 Update feeder floor, Add silkscreen for hand labeling, Fix design rules
    [feederFloor.kicad_pcb]
2023-06-04 Set light diffusion board stackup
    [light-diffusion.kicad_pcb]
2023-06-04 Fix fiducial board design rules, Set stackup, plot settings
    [fiducialBoard.kicad_pcb]
2023-06-04 Set n20 encoder stackup, plot settings
    [n20-encoder.kicad_pcb]
2023-06-04 Add power flags to mobo to fix ERC errors
    [mobo.kicad_sch]
2023-06-04 Set mobo stackup, plot settings
    [mobo.kicad_pcb]
